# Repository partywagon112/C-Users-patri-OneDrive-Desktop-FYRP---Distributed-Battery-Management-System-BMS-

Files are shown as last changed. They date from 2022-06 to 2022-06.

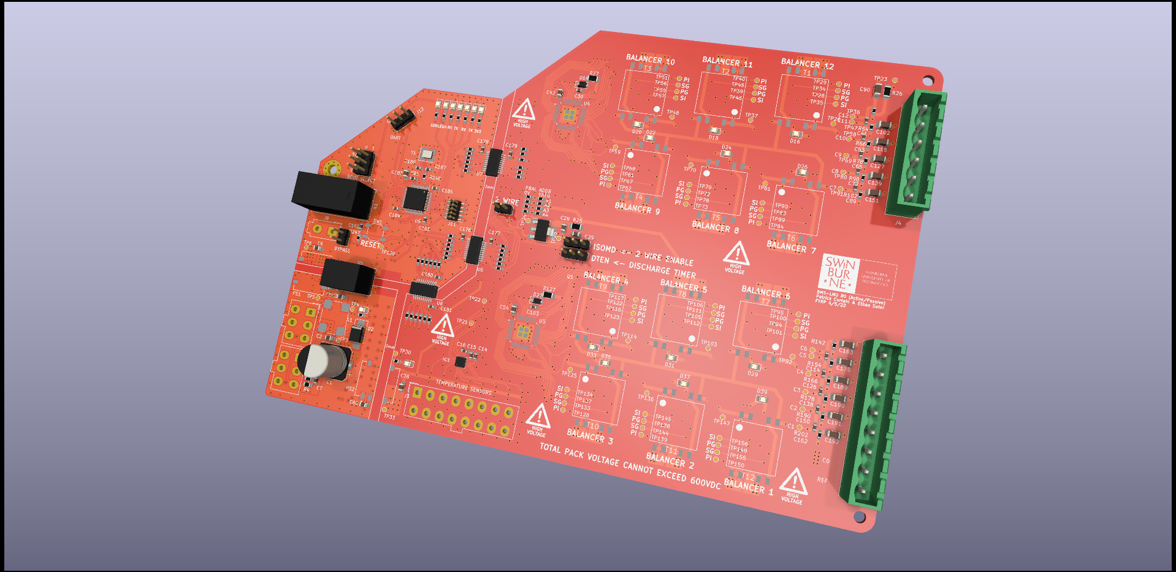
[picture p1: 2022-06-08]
Images/top side render.png

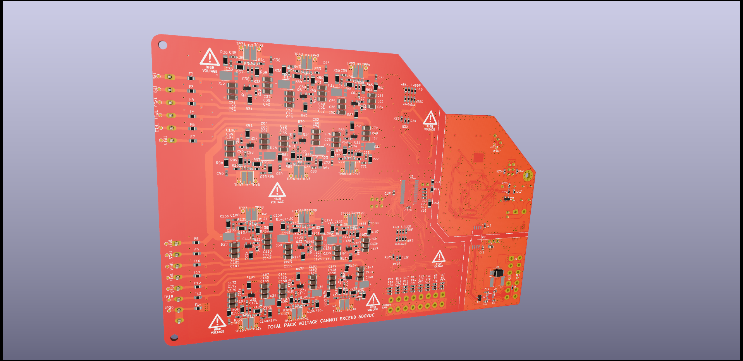
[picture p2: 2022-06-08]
Images/bottom side render.png

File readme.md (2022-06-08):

# Final Year Research Project - Distributed Battery Management System
## Design, Optimisation and System Integration for an Electric Solar Vehicle
### Patrick Curtain & Ethan Suter, Swinburne University of Technology

A project to design a battery management system as a testbed for how one would integrate an active balancing system for an electric vehicle, in particular, an electric solar vehicle.

In this project, a hypothetical system has been conceived for the Swinburne Solar Team electric vehicle and a BMS layed out for how it would function as part of the vehicle. The BMS in question is a multichemistry (0.8-5V), distributed system, comprised of a single gateway (Master) Central Management Unit (CMU) and multiple twelve cell circuit (Slaves) called Local Measurement Units (LMU), connected to the gateway on a private CANBUS. The project makes use of the LTC6811-2 and LTC3300-2, using conventional 4-Wire SPI to make the connection to a control interface more modular.

## BMS-LMU
BMS-LMU

As a proof of concept, a test LMU was produced to perform the specified functions of the BMS-LMU, and documentation included in this repo. This integrates the active and passive balancing units onto a PCB with an STM32F103 performing the local management and CANBUS forwarding functions.

## Acknowledgements
A big thank you to Team Swinburne for the platform and code base used throughout the design of this project. Their work is available: https://github.com/Team-Swinburne

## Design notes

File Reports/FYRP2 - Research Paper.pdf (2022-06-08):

# Distributed Battery Management System (BMS) Design, Optimisation, and System Integration for an Electric Solar Vehicle

## Research Paper - Final Year Research Project (ENG40001)

### Patrick Curtain

Swinburne University of Technology Melbourne, Australia
101109830@student.swin.edu.au

### Ethan Suter

Swinburne University of Technology Melbourne, Australia
102110833@student.swin.edu.au

Abstract—This paper proposes a battery management system that integrates an active balancing system in order to extend the lifetime time of an electric vehicle and minimise wasted energy. The system makes use of a central gateway that functions as the master, and a user configurable number of measurement taps in multiples of

### 12. Whilst there are many automotive grade BMS units

available, very few include an active balancing system, it is the goal of this project to create a template for one that optimises cost, physical space requirements, complexity, performance, and safety. The design context for this system is for the purposes of an SPEV (Solar Powered Electric Vehicle) intended for entry into the World Solar Challenge, however the technology is not limited to this application. Being able to maximise the amount of energy that is wasted is especially beneficial - as current generation EV battery systems age, the delta between the highest and lowest cells will increase, and being able to quickly balance out the issue on the go will prove to be a groundbreaking leap in technology.
Index Terms—SPEV, EV, BMS, Lithium Ion, Lithium Titanate, Electric Vehicles
I. INTRODUCTION
A Battery Management System (BMS) is one of the most important components of a lithium powered electric vehicle. They function to ensure the safety of the pack, preventing dangerous under/overvoltage conditions, preventing component damage and hazardous fail modes. As lithium batteries degrade, their electrical properties change and will charge and discharge at different rates.
The difference between the highest and lowest cell voltage is termed the pack delta, and the aim of balancing is to reduce it as much as possible, typically within the range of tens of milivolts. Battery packs that do not balance contain excess energy that cannot be discharged because if so, the minimum cell voltage will be exceeded [1]. Likewise, the same is true of charging, if the maximum cell voltage will be exceeded, then charging must cease.
The most common method of cell balancing is passive balancing, where the energy from the highest cell is discharged as heat. This practice is inherently wasteful and if the BMS is stored within the accumulator, this also serves as an unwanted source of heat for the pack, wearing the cells out further. Another issue of this strategy is that one is still limited by the lowest cell voltage - all cells are bled down to the lowest cell voltage, a poorly performing cell cannot have energy put into it. Passive balancing is slow, and slower if the thermal limits are exceeded.
Active balancing differs from passive balancing in that is is able to redistribute energy about the pack; higher cells are able to charge lower cells. This process reduces wasted energy and heat in the accumulator. In the case where there is a cell with poor health, it is then possible to siphon energy from this highest cell to extended the life of the pack.

II. BACKGROUND
The Swinburne Solar Team vehicle at present makes use of repurposed Lthium Titanate (LTO) cells acquired in 2018. Lithium Titanate cells have a nominal cell voltage of 2.3V, well below the minimal cell voltage supported by most commercially available BMS units. Furthermore, these cells are from several different sources; they discharge at vastly different rates. Whilst the project would likely transition to LFP (Lithium Iron Phosphate) based cells at a later stage, in the pre-competition phase of the project, budgetary constraints are an ongoing issue; it is likely that large cell deltas will prove to be an issue for some years to come. Cell measurement is not the only challenge in the scope of this design. The changing landscape of solar technology also provides quite a few issues for how to structure an architecture suitable for an extremely wide voltage range. At the moment, the most prevalent flexible cells have a low open cell voltage, around 5.6V [2]; these being connected in series to maximise their voltage output. The most successful cruiser class vehicles in the competition are medium voltage, around 90V to 220V. As this technology improves, it is likely that the voltage will increase rather than decrease to reduce mass [3], and as such, it is necessary to accommodate higher voltages, possibly as high as 400V or 800V. At this voltage, it is unlikely that LTO (Lithium Titanate) cells could be used, as the low nominal cell voltage would mean at least 285 cells would be required in series for 800V, with parallel units required for the extra current carrying and energy. It should be noted that LTO cells do typically support a higher cell current before experiencing failure, however it is unlikely this would not compensate for the extra capacity requirements.
A. Project Goals, Scope, and Research Questions With this context in mind, the following goals were set to guide the design of the system:
- Cell voltage range of at least 0.8V to 4.5V to meet the requirements of most lithium chemistries.
- Accommodate a total pack voltage of up to 600V.
- There should be no unpopulated cell measurement taps; with fewer cells the BMS should be reduced in size.
- Able to manage cells in poor health as efficiently as possible; the reduction of energy waste in balancing.

With so few automotive grade BMS units offering active balancing, this project addresses the gap in research into the feasibility and practicalities of including an active cell balancing system. The primary questions are as follows:
- Is the amount of space required to include an active balancer suitable in such a weight optimised vehicle.
- Is it possible balance the vehicle on the go to extend the life of vehicle.
- How would one approach the design of such a BMS system, and ensure it meets ISO26262 requirements.
- What efficiency gains can this system provide over typical passive-only solution on the market currently?

III. METHODOLOGY
A. State of Charge Estimations
After initial research of existing ways to estimate state of charge early on in the project, it was decided to use a combination of cell voltage readings and coulomb counting [4].
Further research into the cell chemistry available to use for this project (LTO) demonstrated potential challenges with voltage-level based estimations. An LTO discharge graph shown in Figure 1. While the non-linearity is not of direct concern (creating a map of voltages to correspond to charge levels would be trivial), it does result in a large portion of the cell’s discharge cycle occurring over a relatively small voltage delta. This itself can be mostly accounted for but the additional presence of voltage sag complicates this characteristic. A cell experiencing a high current draw that starts to lessen whilst in a shallow-sloped region of its discharge curve could read approximately the same voltage level for 10-20% of the cell’s capacity. Accounting for voltage sag could be done formulaically by establishing a mathematical relationship between the amount of voltage sag occurring at a given capacity level and the amount of current being drawn through that cell [5]. Even accounting for voltage sag, using only instantaneous measurement based estimation will result in SoC readings fluctuating in a dynamic charging/discharging environment. Accurately accounting for voltage sag while current draw changes constantly is a much more difficult task.

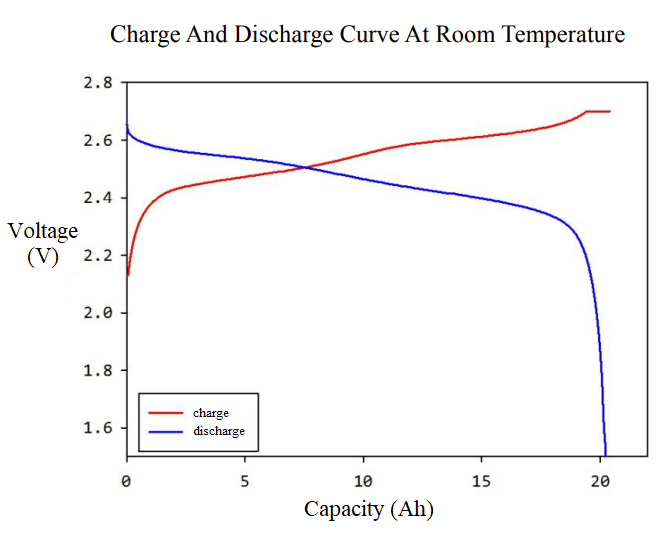
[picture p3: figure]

Fig. 1: Discharge graph of an LTO cell. Note the low cell voltage range. Sorce: data sheet for 16Ah LTO cells in use by the Swinburne Solar Team [6].

Coulomb counting can be achieved by attaching a current clamp to the output, measuring the instantaneous power discharged overtime, and integrating this to find how much energy has been consumed and compare to the pack’s theoretical capacity. Coulomb counting can provide a stable SoC estimation over time, reading cell voltage and current draw multiple times a second and extrapolating energy used. Coulomb counting will result in far more meaningful SoC readouts during periods of high/fluctuating current draw. A drawback of this method is that it can drift over time, due to not being able to account for energy wasted as heat and a lack of absolute reference. In nautical terms, this method is analogous to dead reckoning.

With these two estimations of the packs health, a weighting can be applied to the validity of each estimation. With high current discharge, the effect of voltage sag can be mitigated by relating current discharge to the weighting of the coulomb counting method; During periods of high current draw the coulomb counting estimation will be weighted more.

After this methodology has been implemented in the BMS a formula will have been developed to represent stage of charge.

B. Modular Stack Design

In order to achieve the target of space optimisation, a distributed architecture was pursued to provide scalable device size across different battery configurations. This architecture abstracts away the functionality of the BMS chips, making it simpler to change out modules, iterate designs, and refine the project further.
A similar modular architecture is explored by Henar Cailang, Caliway, and Wanson, for a small form BMS for use in a Motorbike, using a masterslave system [7]. Similarly, the BMS concept of this project is to be designed is broken up into the same style of system, with a Central Management Unit (CMU) as the gateway that oversees many Local Measurement Units (LMU), which each attend to a particular group of cells. The main disadvantage of this scheme is that fault detection becomes inefficient, as communication becomes reliant on persistent updates between units, requiring a watchdog, and whilst the absence of a module may not mean a fault, one shall be triggered, and little more information can be gained [7].
C. Cell Measurement, Active vs. Passive Balancing, and ASICs

Passive balancing is conceptually quite simple; Whilst a battery is charging, the highest cell is discharged to match the lowest cell, and this process repeats until all are within a certain delta. This is achieved by simply discharging energy from the cell as heat, light, or kinetic energy, etc.
Active balance utilises the excess energy from the highest cell to charge the lowest cell. In this way, energy has been redistributed, not lost, thus minimising wasted energy. This is usually achieved with some form of coupling, to connect the highest to the lowest cell, and using that to equalise the two cells. This is usually done by isolating both cells from the stack, and connecting them in parallel, with circuitry that allows the control of current flowing between the cells to prevent large loads causing degradation for both cells involved. In addition to gains in energy conservation this method can also achieve more than double the effective rate of balancing, since the two most outlying cells are being equalised to an average cell voltage simultaneously, rather than one cell being discharged all the way down to the lowest cell voltage at a time.
In order to simplify the complexity and overall size of the final output, it was decided very early into the project, that a pre-designed BMS IC would be used. These ASICs typically integrate various forms of cell measurement to autonomously perform balancing with little external input required. Two ICs were sought to solve this issue, based on research from an earlier literature review [4], the LTC6811, and the LTC3300. These two BMS ICs are designed to work together to achieve the passive and active balancing requirements outlined for this project [8].

IV. DISCUSSION

Given cost and time restraints, the project was reduced in scope from it’s original plans such that a only the LMU would be designed, and a single functional LMU be produced to serve as a proof of concept. The LMU is the most important part of this project, representing the most complex amount of circuitry and the largest portion of functionality (for both hardware and software). The CMU’s functionality can be containerised in software; it can be simply a CANBUS gateway with some high side drivers to run the contactors, and simulating its functionality would be relatively trivial.

A. Active Balance Circuit Design
The active and passive circuits follow the design recommendations outlined by the manufacturer of the ASICs [9] [8], The passive circuit makes use of a small P-Channel FET that is able to handle around 100-500mA, and a small resistor. A LED circuit has been added to indicate which cells are balancing. The active balance circuit requires two high current switching FETs, with the secondary of each transformer being connected to a common charge rail(denoted as BOOST in the schematic). To help decrease the BOM, a dual channel N-FET with a low RDS, and low gate capacitance was used. These FETs will switch at a frequency of 2kHz, with a typical charge current of 2-4A. The way in which this circuit operates, is that the primary side of the highest voltage cell’s module will be coupled onto the secondary side. At the same time, the lowest cell’s primary coil will be switched at high speed to enable current flow. The LTC3300 manages this control loop, and a small measurement tap is attached to a shunt resistor connected to the drain of each FET, closing the control loop and providing the required hysteresis. The port on the right extends to the active and passive cell measurement inputs, and makes use of a simple RC filter to the adjacent cell (Cell measurements are differential), and the ground reference.

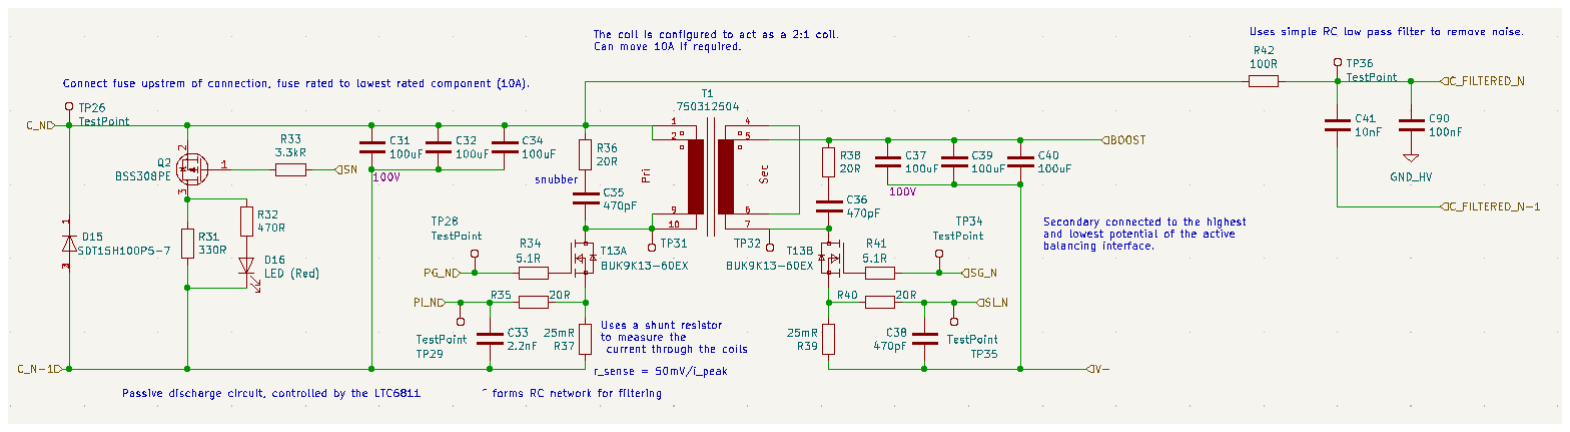
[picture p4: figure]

Fig. 2: The circuit used on each cell input, the left part includes reverse protection diode, and the passive balance circuit, a small SOT23 P-Channel FET, and a 330Ω resistor. The right half includes an isolated 2:1 10A transformer and N-Channel FETs with a connection to the boost rail.

B. PCB Design

The PCB for the LMU is significantly larger than original concepts for the design earlier in the project. The original idea was to create a daughterboard with a SODIMM form factor that would hold either 2(single-sided) or 4(double-sided) active balancing modules, that would connect to a backplane that would attach directly to the terminals of the cells [4]. in this way, should the active system be too large, modules could simply be removed.

C. Isolation, Safety, and Grounding

Grounds serve two main purposes, for protecting the integrity of signals, and protecting systems and users in case of a fault [10]. In the vehicle, an IMD (Isolation Monitoring Device) is used to ensure that no more than 2mA is able to pass from the high voltage system into the vehicles system. A device such as the ISOMETER IR155-3204 will be connected with the ability to break power to the main accumulators on fault [11]. This protects against the mechanical failure of various parts of the powertrain, where contact is made when insulation

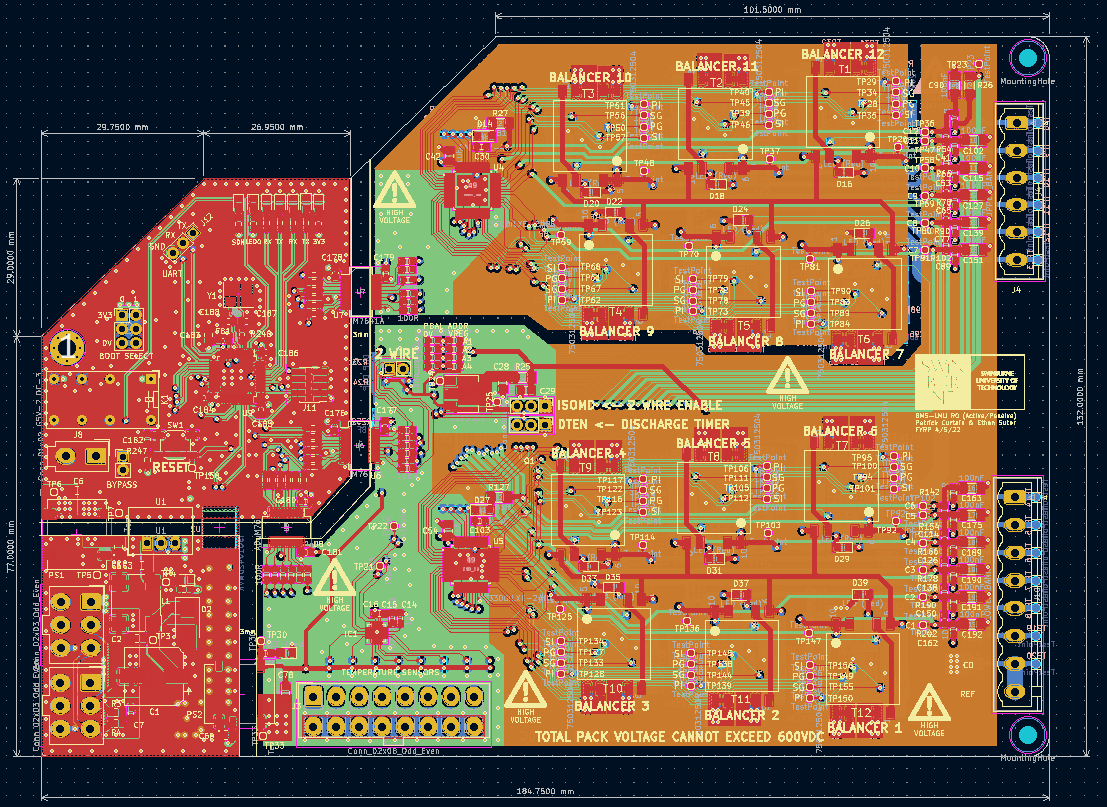
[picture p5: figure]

Fig. 3: The PCB designed to perform the functions described by the LMU.


Fig. 4: Rendering of the top side of the LMU PCB.

is not present or has fatigued, as well as the electrical failure of the various ICs and DC-DC converters that are used to isolate the barrier.
Of great concern in the development of this BMS was its ability to handle high voltages. A safety isolation barrier of 3mm has been included to allow the device to meet the IPC2221B high voltage clearance requirements [12].
In order to simplify the architecture and avoid being locked into using Linear Technology’s proprietary interpretation of SPI, isoSPI, a simple series of simple high speed digital isolators is to be use. The primary advantage of this scheme is that inter stack connections do not need to be adjacent since the communication interface is connected to the same ground as the vehicle. As such, the pack can be split across the vehicle without much additional wiring. There is some danger associated with extending the ground planes used for high voltage. A large

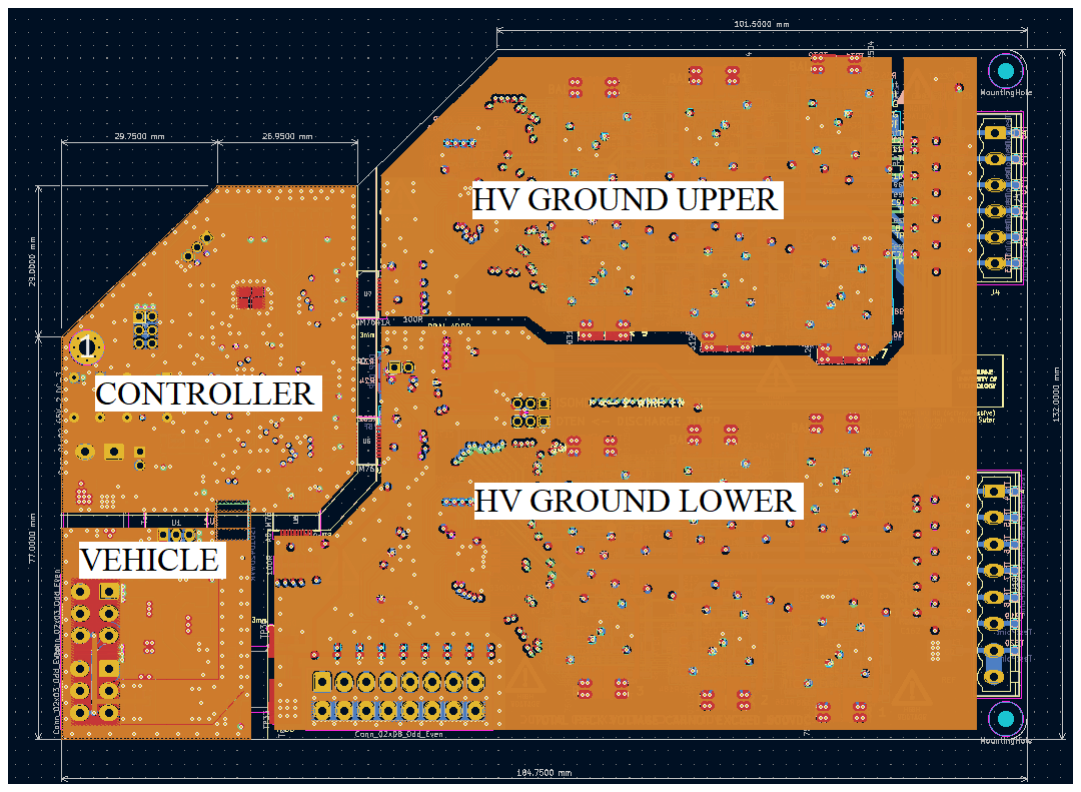
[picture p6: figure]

Fig. 5: The different ground planes used to break up the PCB. Note that each of these zones is galvanically isolated except for HV ground upper and lower, explained in Section IV-D.

plane is a huge physical target and risks the operator or assembler making contact with the high voltage plane. Of course, during assembly, high voltage gloves must always be warn and ample warnings are listed on both sides of the board, however additionally, these planes have been restricted to the internal layers of the PCB. Therefore the risk is reduced to only traces and components.

D. EMC Considerations

There are several issues that face the design of the HV system; balancing cost, physical size, and ensuring board maintains good electromagnetic immunity. The active balancers switch high currents at a relatively high frequency, as such they pose a risk to the other ICs as they will be the primary source of noise affecting cell measurement. The emissions of the device will directly affect the immunity of the other ground. The standard defence against this issue is to increase the size of the return path, and place that as close as possible to the signal. All signal layers are directly adjacent to a ground layer to minimise issues [3].
A small RC filter is utilised on the board. Due to space constraints, this was placed at the input of each voltage tap to the board, however the way to best optimise the strength of the filter would be to place it as close as possible to the input of the cell measurement IC.
The highest six cells of the stack are referenced relative to two points. The first reference is for the cell measurement the lowest potential of the stack. Whilst measurements are performed in a differential manner, the passive balance IC itself is grounded to the lower potential ground, and as such lines to the point, must be shielded to that ground. The second ground is relative to the reference of the sixth cell in the stack.
A proposed alternative strategy was to make use of a six layer stackup, with the cell signal layer being adjacent to a layer for the active ground, and another layer dedicated to only the HV ground. This was dismissed to reduce cost.
There is an additional ground included on each LMU that is galvanically isolated from the vehicle ground and the HV ground, that contains the microcontroller and logic. This is done to provide an extra level of immunity for the mission critical microcontroller. This practice is well endorsed by SAE design guidelines as it provides a good way to break up critical areas of the vehicle [3]. Even in the case of a communication failure with the rest of the vehicle, the microcontrollers integrity must be maintained. Given the high amount of switching noise generated by the powertrain, one should expect immunity to be an issue. CISPR 25 is the typical automotive standard that is used to quantify how much the device radiates, and its immunity [13], and as testing progresses, some parts of this regime may be tested to gain insight into the performance of the design.
V. CONCLUSION
With the testing of the LMU commencing in the next week on a live battery stack, it will be interesting to begin qualifying and quantifying the proposed solution. The challenges to reach this point have been great, with an underestimation of the space required for the additional active balancing circuitry being the primary issue, and causing the most delay. As discussed earlier, a good proposal would be to build a system where it is possible to remove the active balancing circuitry where not required. This has several advantages, such as minimising the width and length of the PCB, in exchange for better using the height, a usually under utilised part of the volume.
Various logistical issues have greatly affected component selection on the PCB, and as such, many parts have been interchanged since the initial schematic conception in late 2021. In its current state however, this project is close to producing a system that is able to outperform many of the automotive BMS that are available, and maximise the running time of the solar powered electric vehicle it which it will be used.

REFERENCES

[1] J. Cao, N. Schofield, and A. Emadi, “Battery balancing methods: A comprehensive review,” in 2008 IEEE Vehicle Power and Propulsion Conference. IEEE, 2008, pp. 1–2.
[2] M. A. Green, K. Emery, Y. Hishikawa, W. Warta, and E. D. Dunlop, “Solar cell efficiency tables (version 45),” Progress in photovoltaics, vol. 23, no. 1, pp. 1–9, 2015.
[3] S. Davis, Managing electric vehicle power, ser. SAE Deep Dive. Warrendale, Pennsylvania: SAE International, 2020.
[4] C. P. Suter, E., “Distributed battery management system (bms) design, optimisation, and system integration for an electric solar vehicle - progress report,” 2021.
[5] J. Chiasson and B. Vairamohan, “Estimating the state of charge of a battery,” IEEE Transactions on Control Systems Technology, vol. 13, no. 3, pp. 465–470, 2005.
[6] “Osn power: Lmo/lto datasheet 16ah (13110216),” 2010.
[7] H. M. O. Canilang, A. C. Caliwag, and W. Lim, “Design of modular bms and real-time practical implementation for electric motorcycle application,” IEEE transactions on circuits and systems. II, Express briefs, pp. 1–1, 2021.
[8] “Ltc6811-1 datasheet,” 2022. [Online]. Available: https: //www.analog.com/en/products/ltc6811-1.html
[9] “Ltc3300-2 datasheet,” 2022. [Online]. Available: https: //www.analog.com/en/products/ltc3300-2.html
[10] H. W. Ott, Electromagnetic compatibility engineering, ser. Wiley Online Library ebooks. Hoboken, N.J: John Wiley Sons, 2009.
[11] “Bender isometer ir155-3203/ir1553204 datasheet,” 2022.
[Online]. | Available: | https://www.bender.de/en/products/
insulation-monitoring/isometer ir155-3203ir155-3204 (https://www.bender.de/en/products/insulation-monitoring/isometer_ir155-3203ir155-3204)
[12] T. G. D. 31b) of the Rigid Printed Board Commitee (D-30) of IPC, IPC-2221B: Generic STandard on Printed Board Design. IPC, 2012. [Online]. Available: https: //www.ipc.org/TOC/IPC-2221B.pdf
[13] V. Rodriguez, “Automotive component emc testing: Cispr 25, iso 11452-2 and equivalent standards,” IEEE electromagnetic compatibility magazine, vol. 1, no. 1, pp. 83–90, 2012.

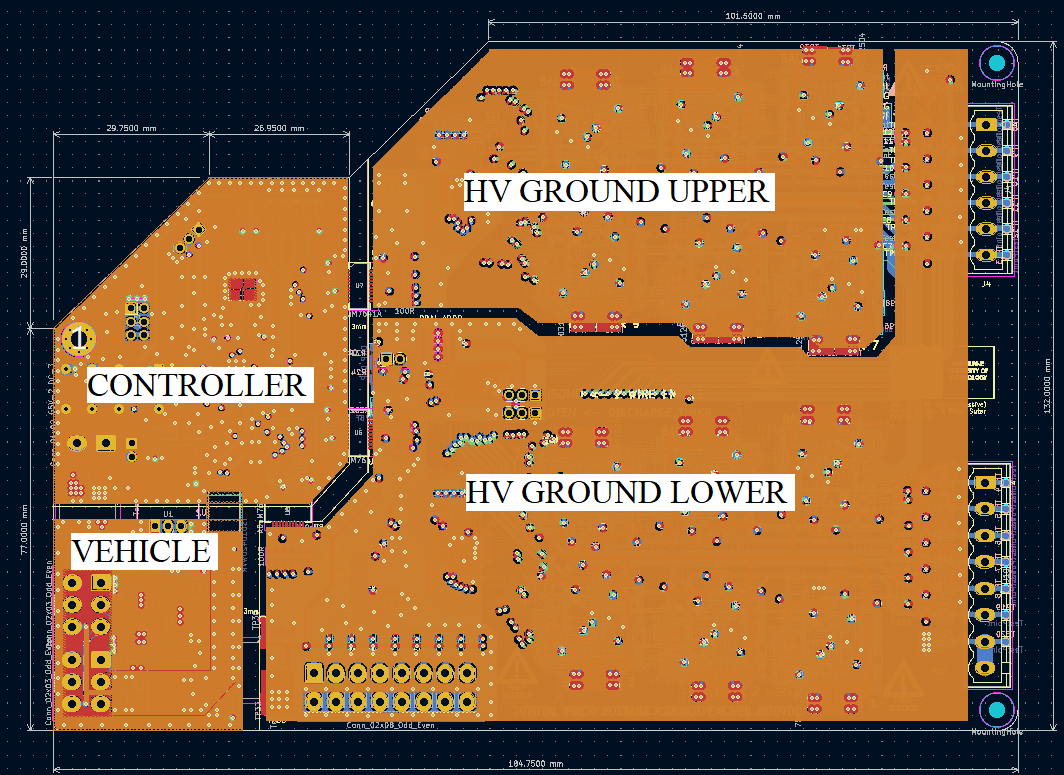
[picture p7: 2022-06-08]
Images/ground strategy labelled.png

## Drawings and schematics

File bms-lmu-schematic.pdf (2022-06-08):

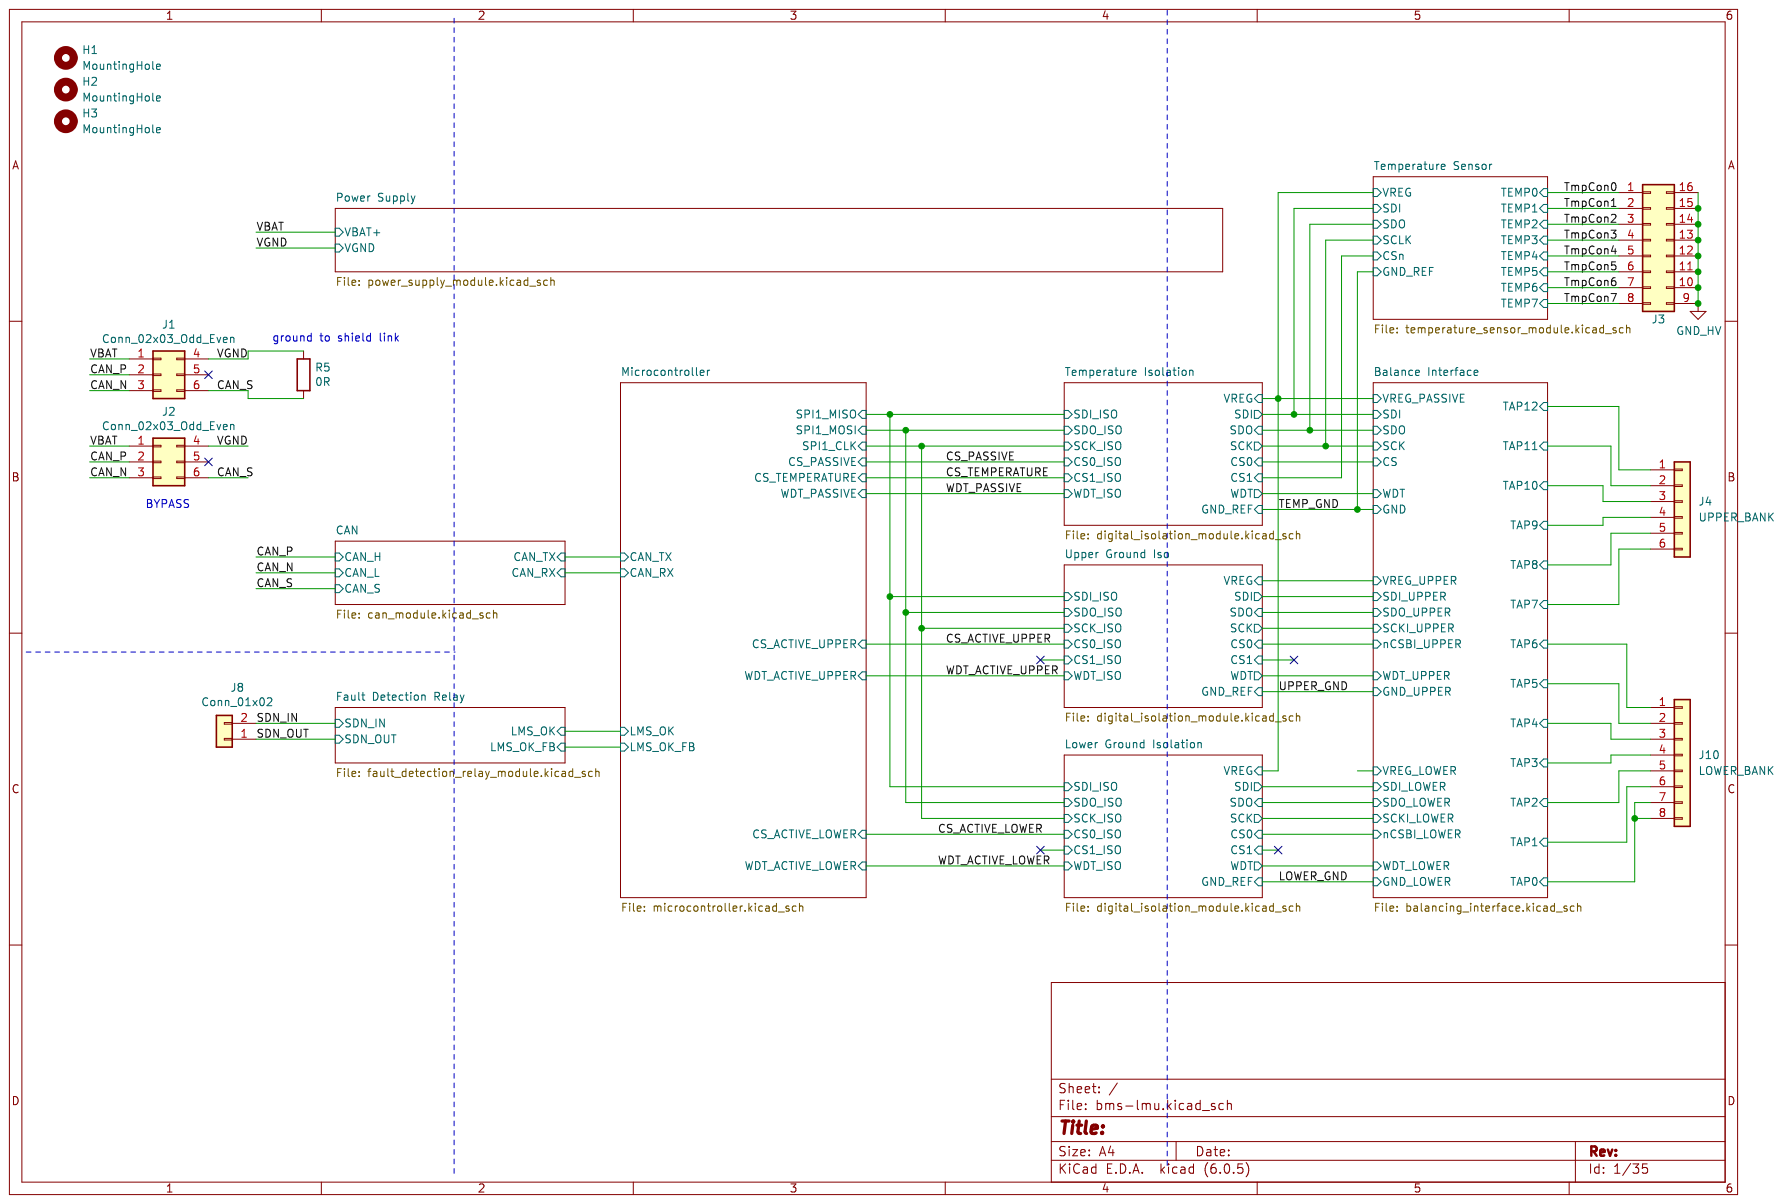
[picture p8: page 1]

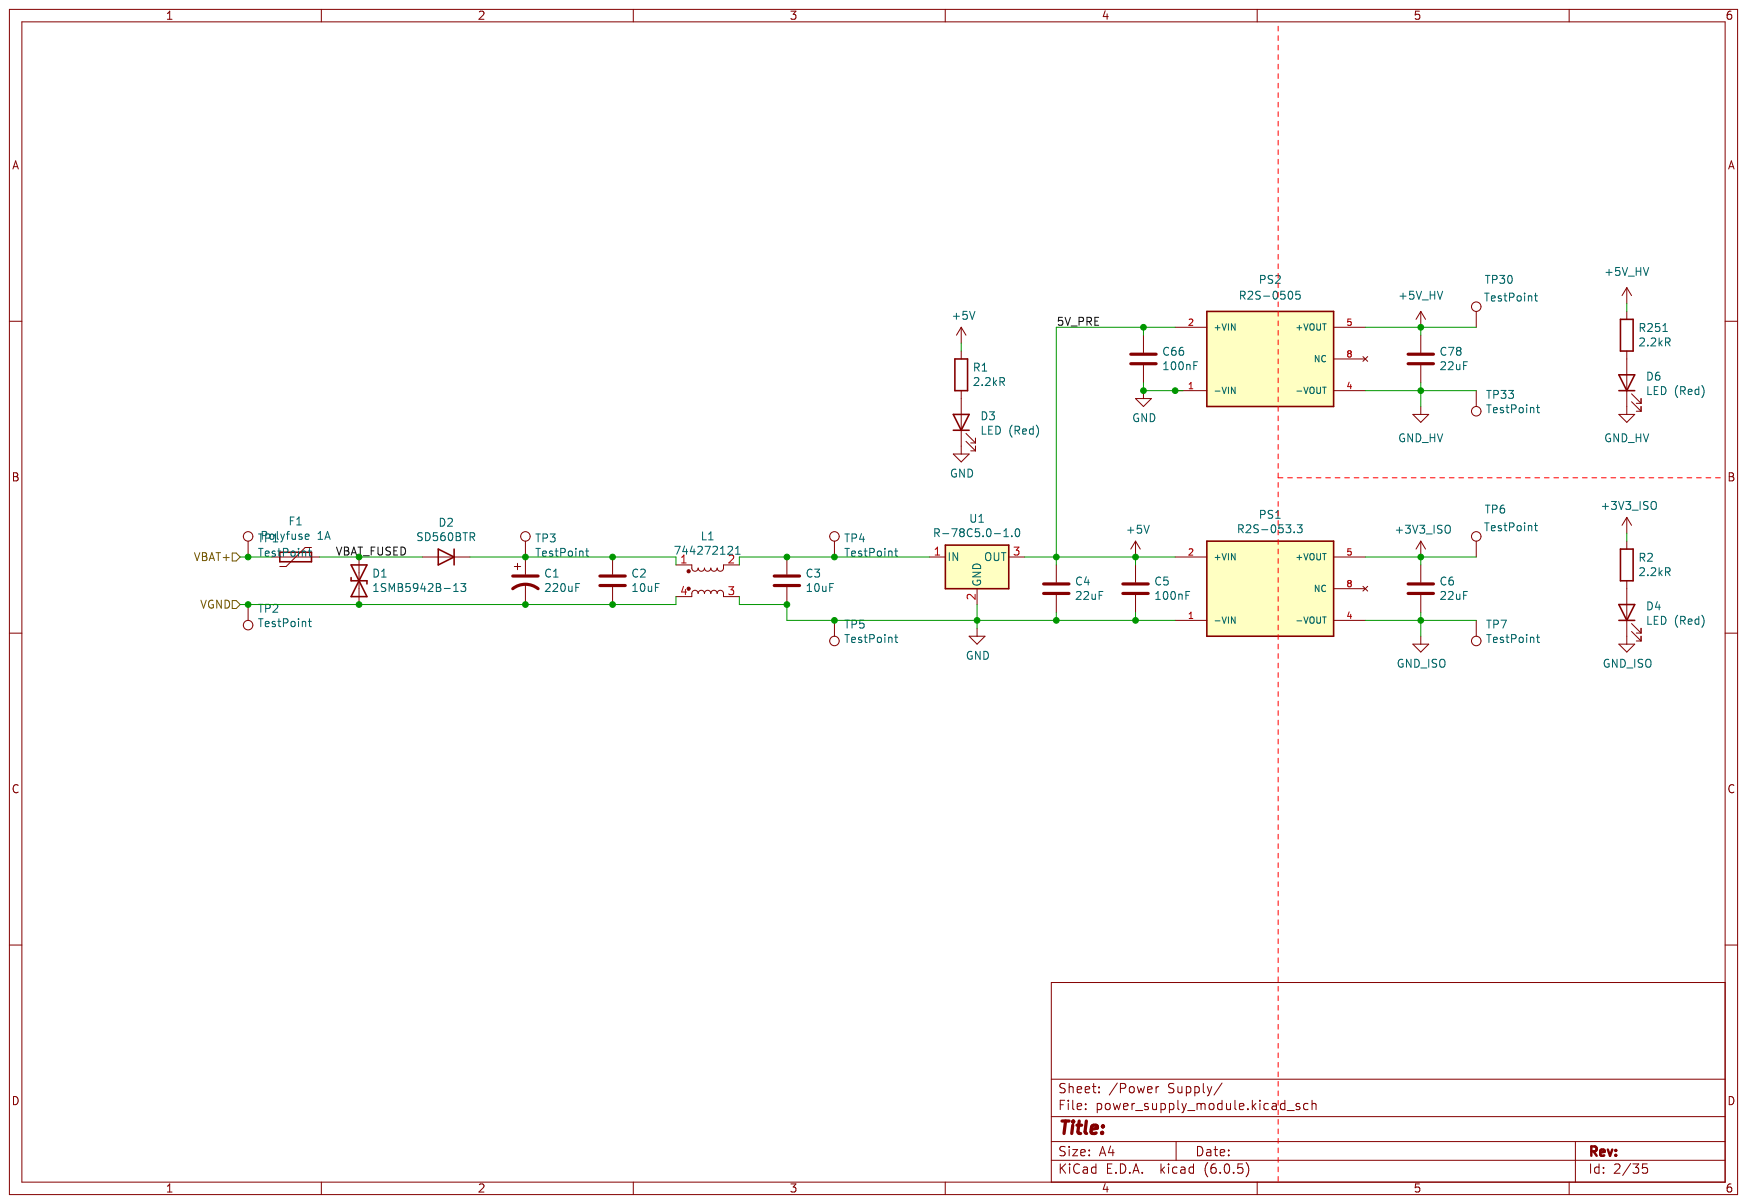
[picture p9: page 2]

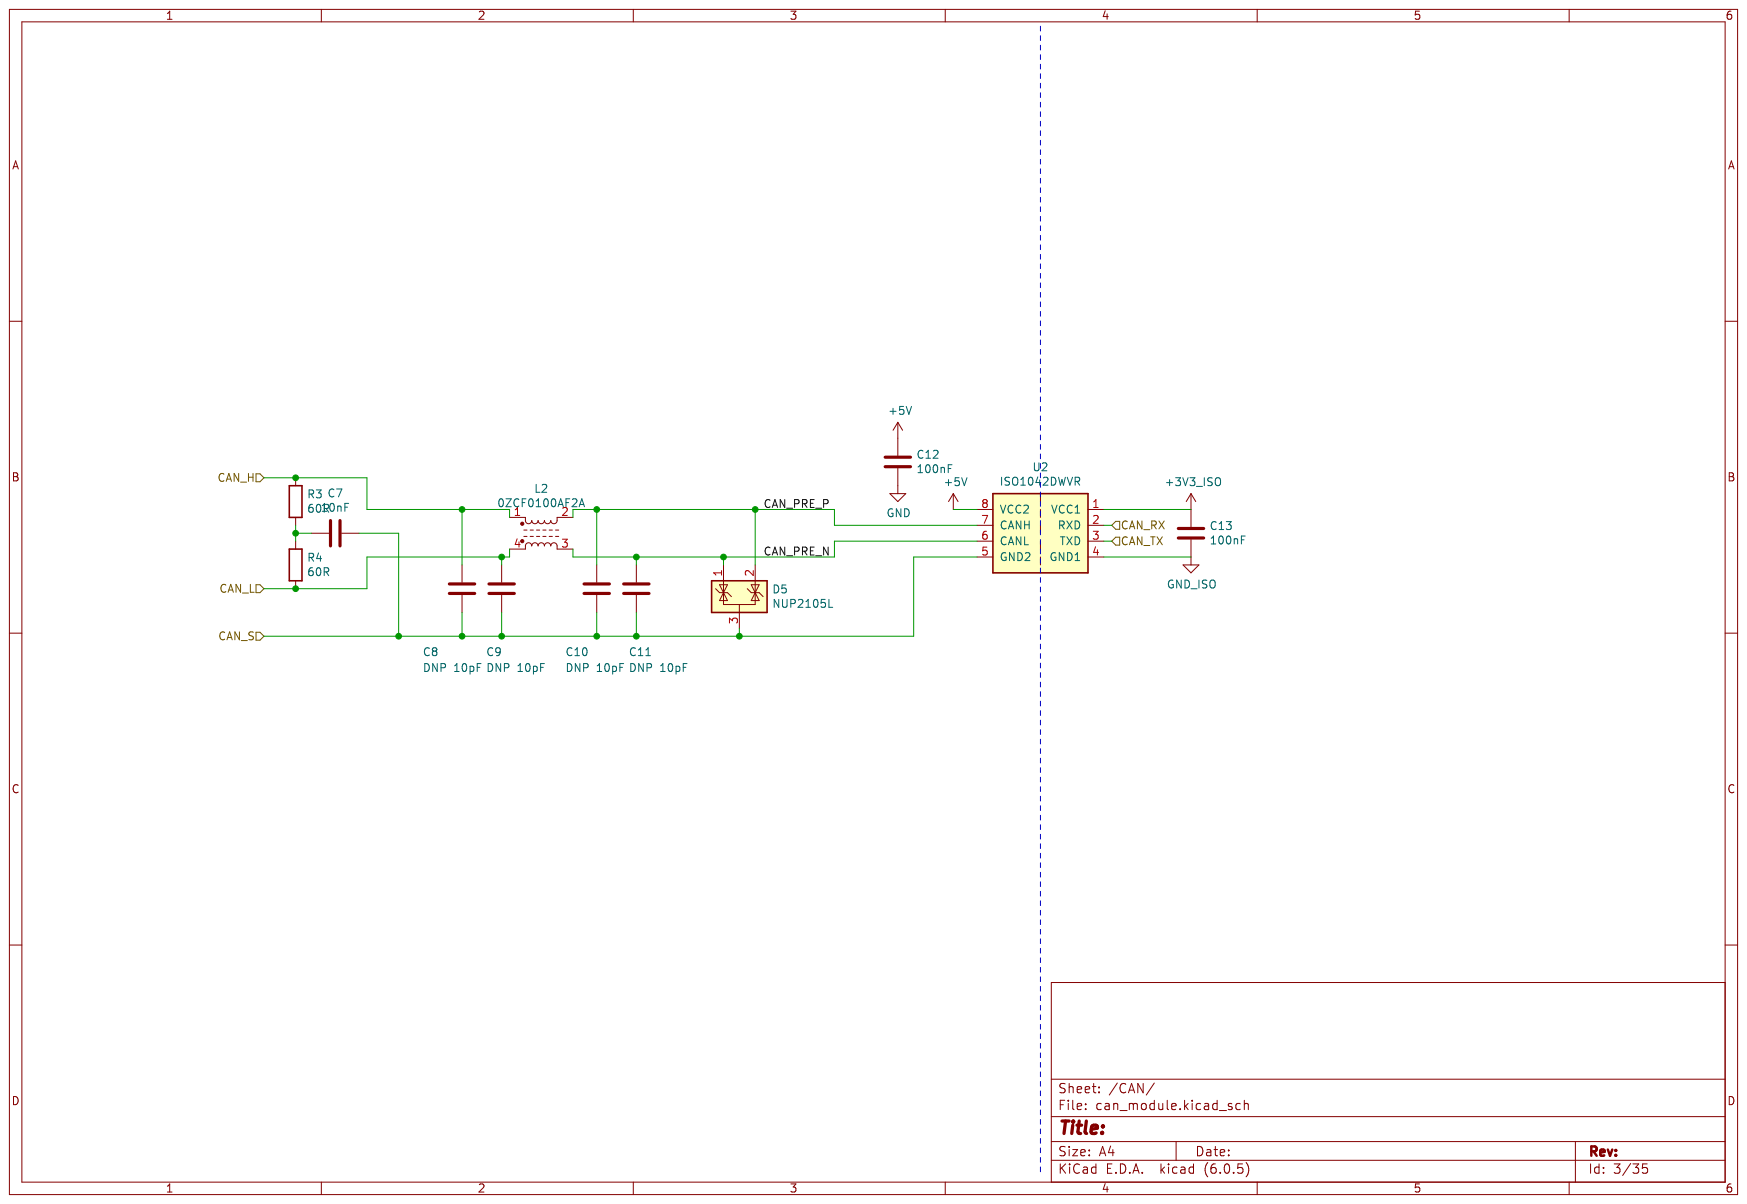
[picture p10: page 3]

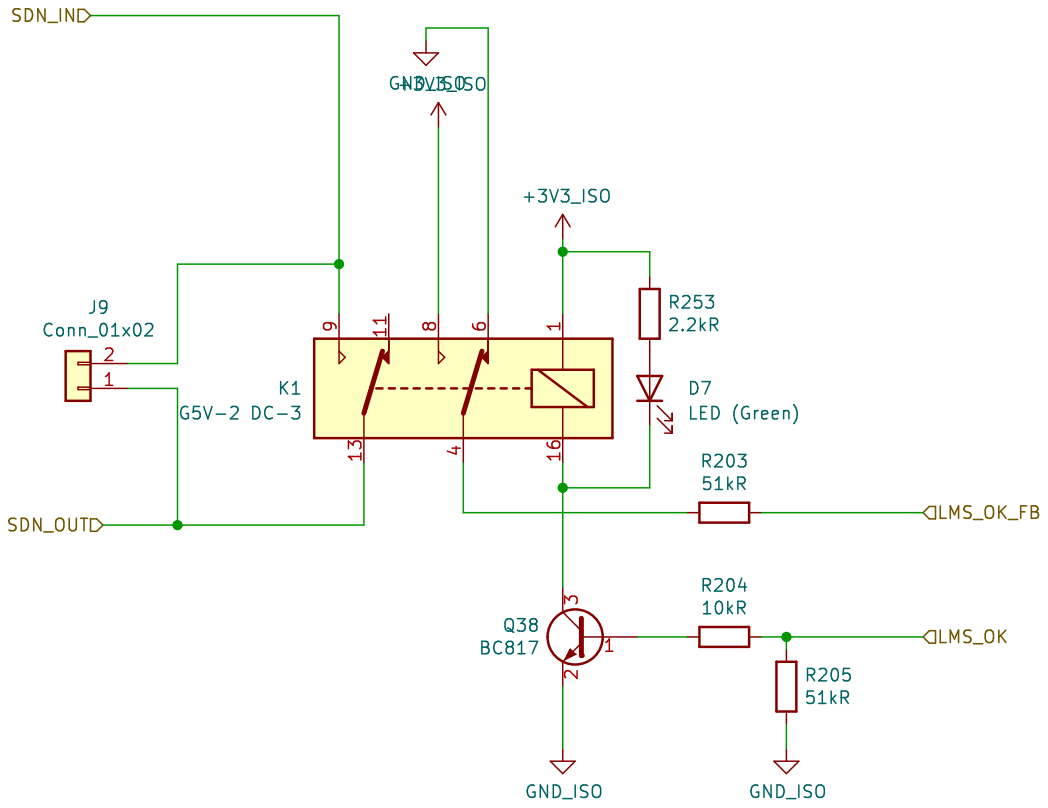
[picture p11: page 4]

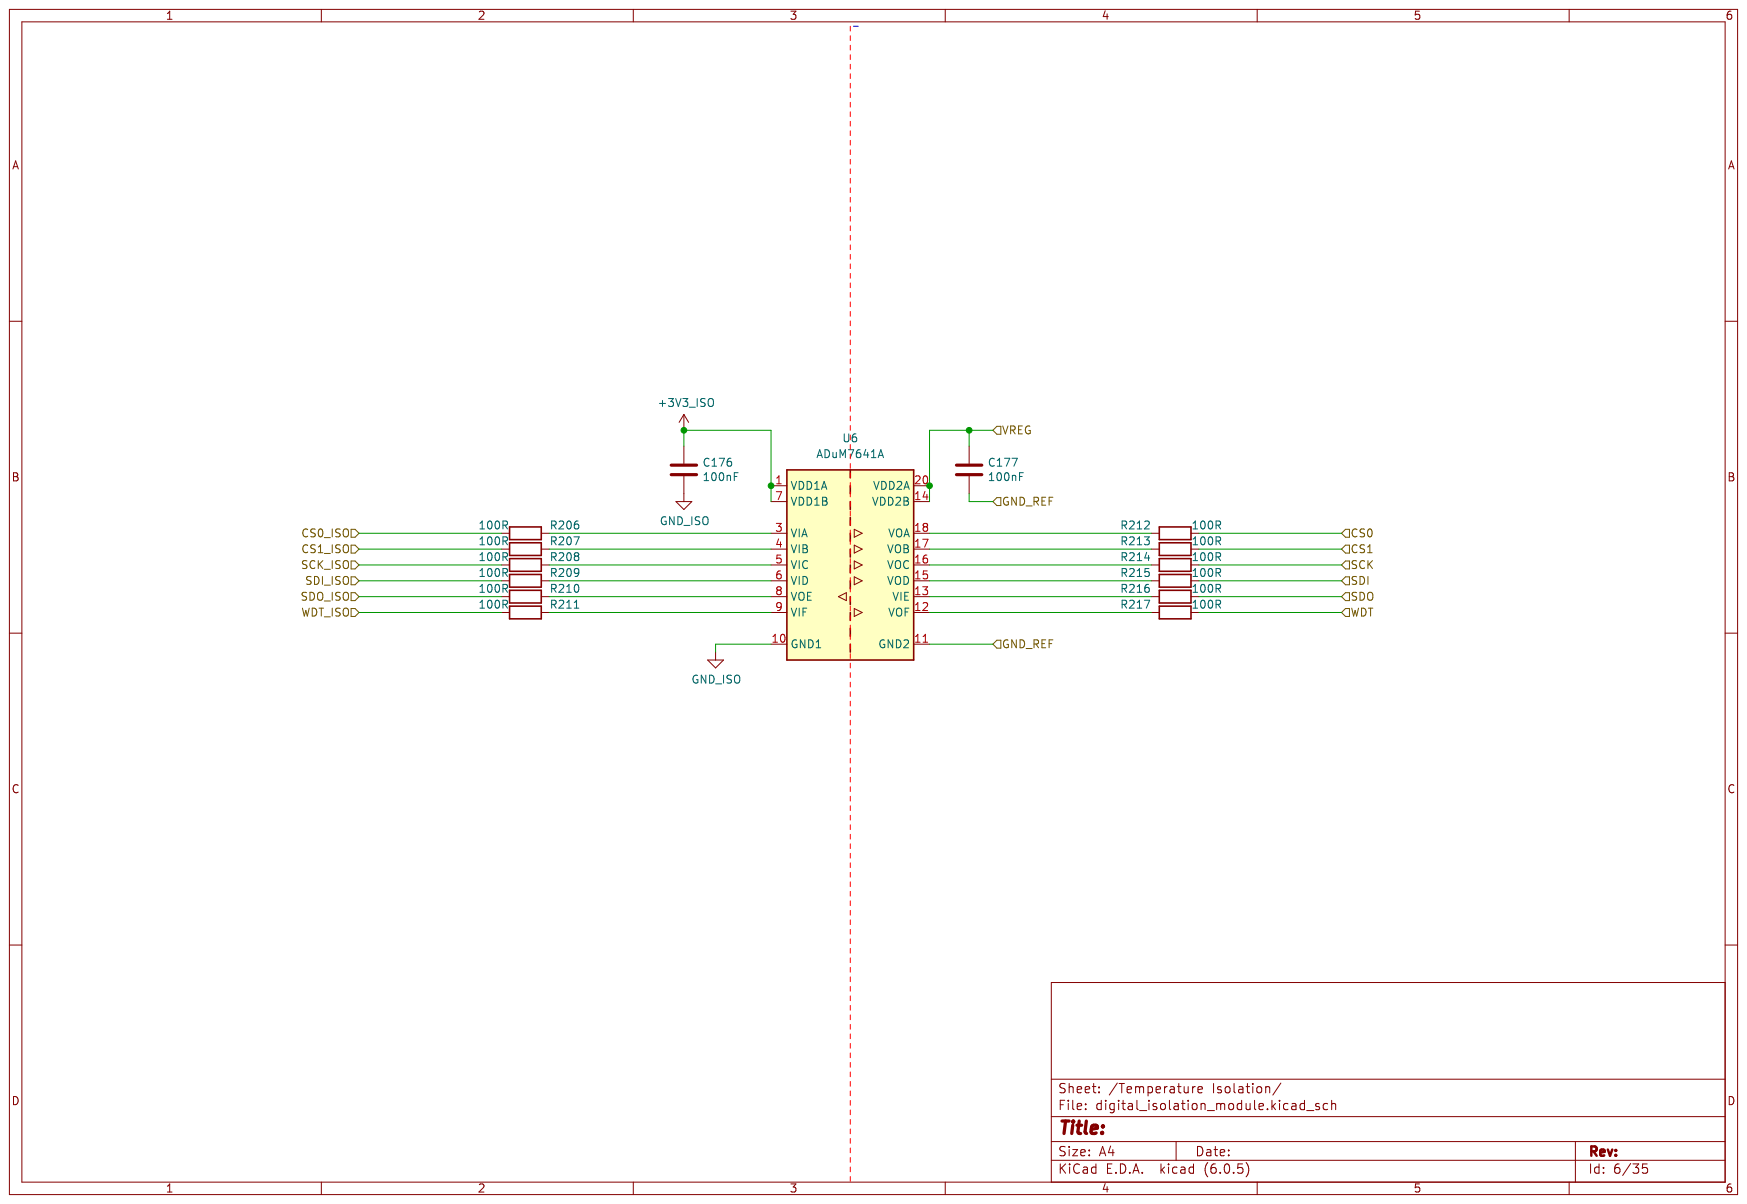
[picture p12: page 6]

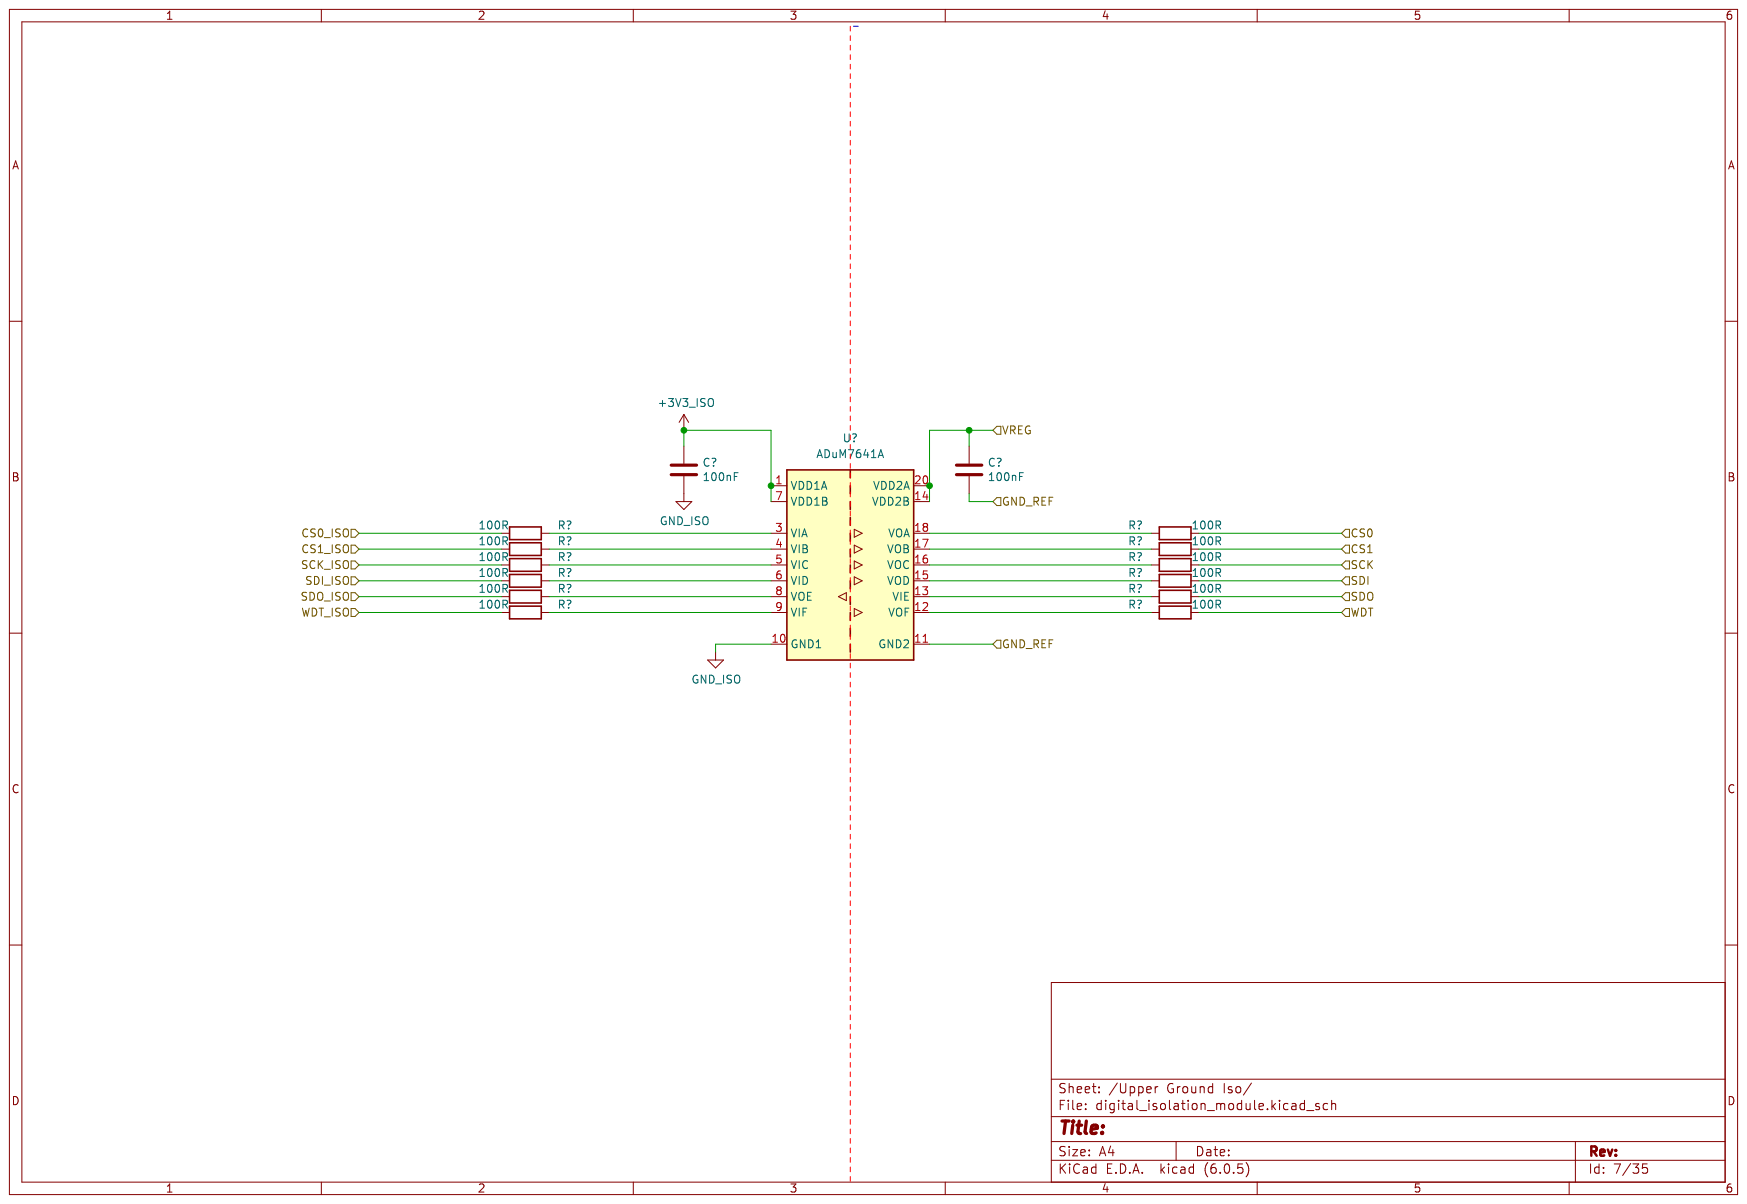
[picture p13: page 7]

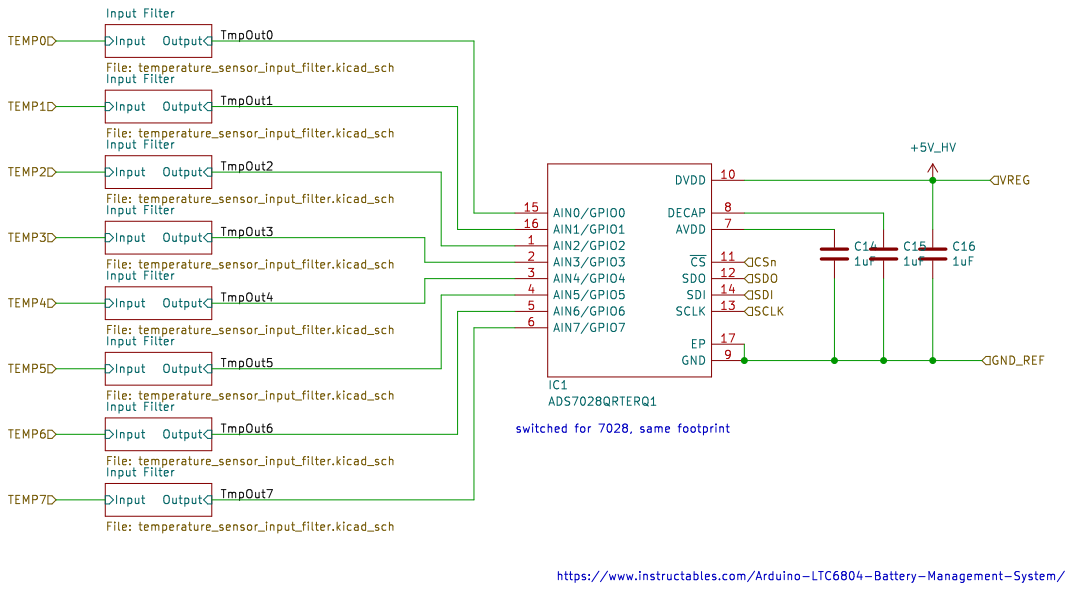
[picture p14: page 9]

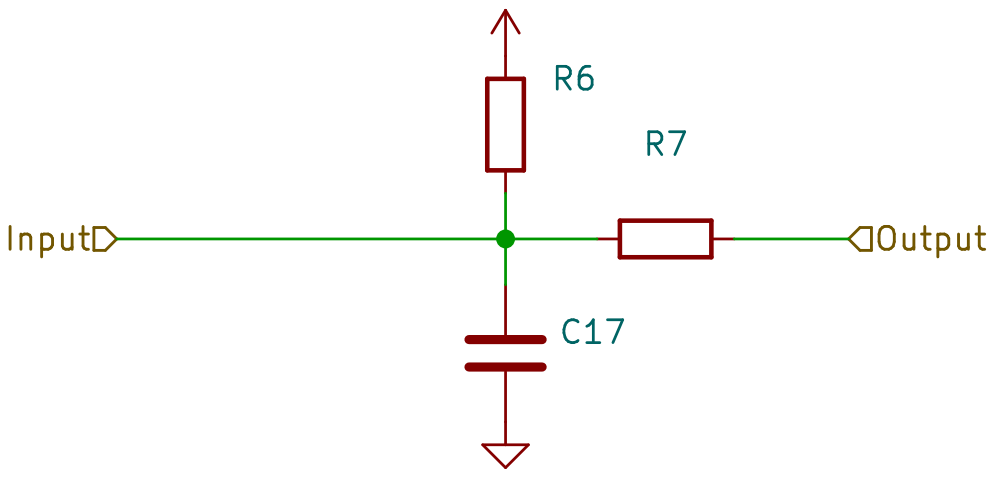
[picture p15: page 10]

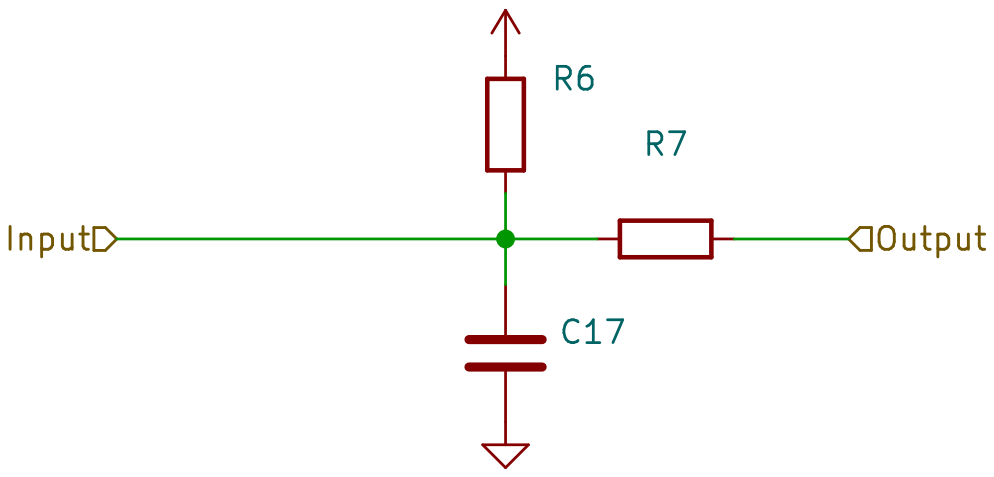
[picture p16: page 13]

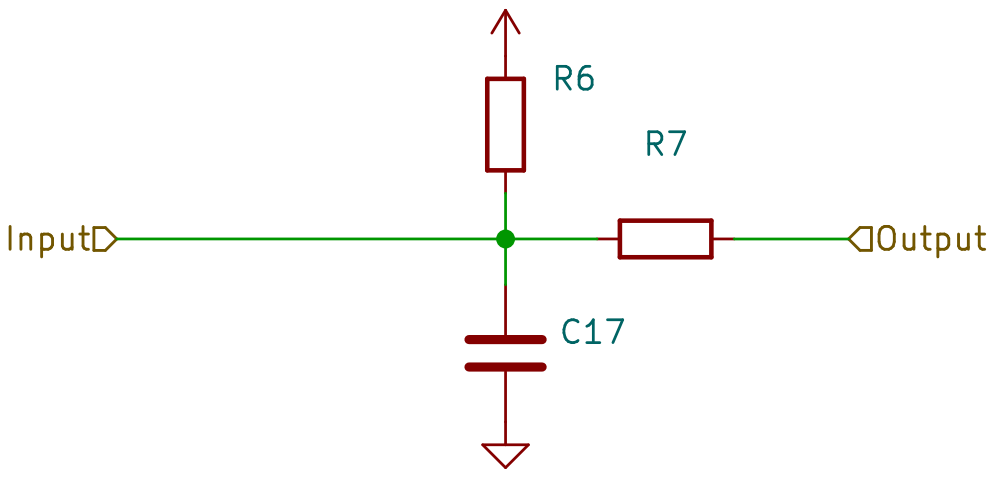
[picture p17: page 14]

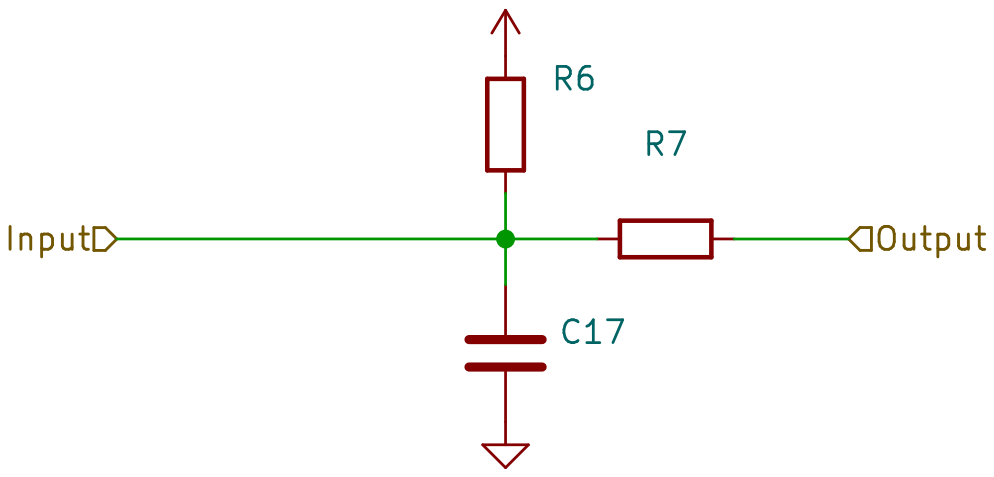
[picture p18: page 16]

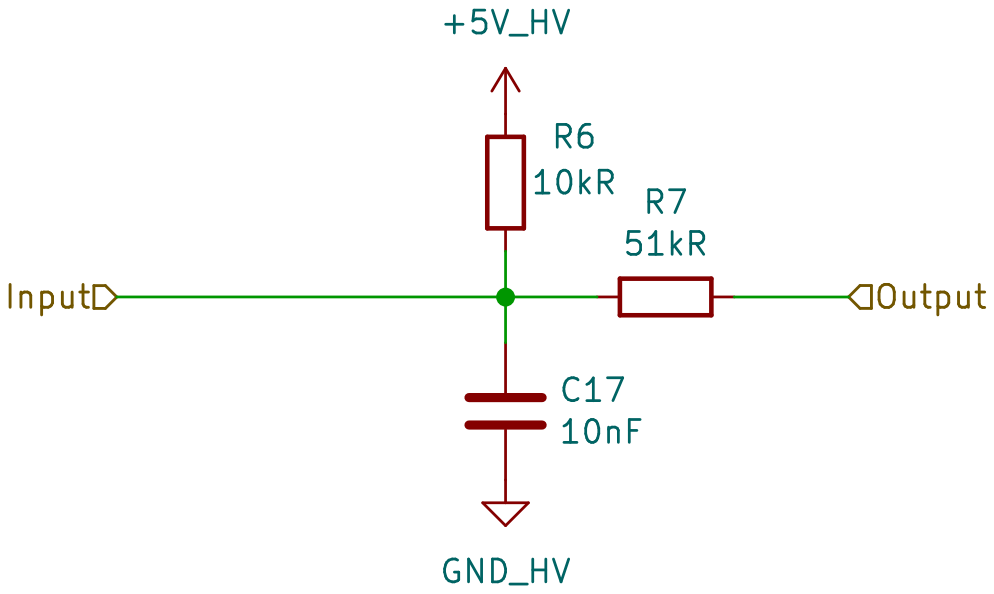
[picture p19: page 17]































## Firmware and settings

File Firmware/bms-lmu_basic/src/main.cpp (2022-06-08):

/*! Analog Devices DC2259A Demonstration Board. 
* LTC6811: Multicell Battery Monitors
*
*@verbatim
*NOTES
* Setup:
*   Set the terminal baud rate to 115200 and select the newline terminator.
*   Ensure all jumpers on the demo board are installed in their default positions from the factory.
*   Refer to Demo Manual.
*
*USER INPUT DATA FORMAT:
* decimal : 1024
* hex     : 0x400
* octal   : 02000  (leading 0)
* binary  : B10000000000
* float   : 1024.0
*@endverbatim
*
* https://www.analog.com/en/products/ltc6811-1.html
* https://www.analog.com/en/design-center/evaluation-hardware-and-software/evaluation-boards-kits/dc2259a.html
*
********************************************************************************
* Copyright 2019(c) Analog Devices, Inc.
*
* All rights reserved.
*
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
* THIS SOFTWARE IS PROVIDED BY ANALOG DEVICES "AS IS" AND ANY EXPRESS OR
* IMPLIED WARRANTIES, INCLUDING, BUT NOT LIMITED TO, NON-INFRINGEMENT,
* MERCHANTABILITY AND FITNESS FOR A PARTICULAR PURPOSE ARE DISCLAIMED.
* IN NO EVENT SHALL ANALOG DEVICES BE LIABLE FOR ANY DIRECT, INDIRECT,
* INCIDENTAL, SPECIAL, EXEMPLARY, OR CONSEQUENTIAL DAMAGES (INCLUDING, BUT NOT
* LIMITED TO, INTELLECTUAL PROPERTY RIGHTS, PROCUREMENT OF SUBSTITUTE GOODS OR
* SERVICES; LOSS OF USE, DATA, OR PROFITS; OR BUSINESS INTERRUPTION) HOWEVER
* CAUSED AND ON ANY THEORY OF LIABILITY, WHETHER IN CONTRACT, STRICT LIABILITY,
* OR TORT (INCLUDING NEGLIGENCE OR OTHERWISE) ARISING IN ANY WAY OUT OF THE USE
* OF THIS SOFTWARE, EVEN IF ADVISED OF THE POSSIBILITY OF SUCH DAMAGE.
*******************************************************************************/

/*! @file
    @ingroup LTC6811-1
*/

/*
NOTES
 Setup:
   Set the terminal baud rate to 115200 and select the newline terminator.
   Ensure all jumpers on the demo board are installed in their default positions from the factory.
   Refer to Demo Manual DC2259.

USER INPUT DATA FORMAT:
 decimal : 1024
 hex     : 0x400
 octal   : 02000  (leading 0)
 binary  : B10000000000
 float   : 1024.0
 */

#include <Arduino.h>
#include <stdint.h>
#include "Linduino.h"
#include "LT_SPI.h"
//#include "LT_I2C.h"           // Hardware I2C driver
//#include "QuikEval_EEPROM.h"
#include "UserInterface.h"   // serial interface routines to communicate with the user
#include "LTC681x.h"
#include "LTC6811.h"
#include <SPI.h>

#define ENABLED 1
#define DISABLED 0

#define DATALOG_ENABLED 1
#define DATALOG_DISABLED 0

void print_menu();
void print_cells(uint8_t datalog_en);
void print_aux(uint8_t datalog_en);
void print_stat();
void print_open();
void print_config();
void print_rxconfig();
void print_comm();
void print_rxcomm();
void print_pwmconfig();
void print_rxpwmconfig();
void print_sctrl();
void print_rxsctrl(); 
void print_statsoc();
// void print_aux1();
void print_aux1(uint8_t datalog_en);
void check_error(int error);
void print_pec();
void serial_print_hex(uint8_t data);
char get_char();
void run_command(uint32_t cmd);
void measurement_loop(uint8_t datalog_en);

/**********************************************************
  Setup Variables
  The following variables can be modified to
  configure the software.
***********************************************************/
const uint8_t TOTAL_IC = 1;//!< Number of ICs in the daisy chain

//ADC Command Configurations. See LTC681x.h for options.
const uint8_t ADC_OPT = ADC_OPT_DISABLED; //!< ADC Mode option bit
const uint8_t ADC_CONVERSION_MODE = MD_7KHZ_3KHZ; //!< ADC Mode
const uint8_t ADC_DCP = DCP_ENABLED; //!< Discharge Permitted 
const uint8_t CELL_CH_TO_CONVERT = CELL_CH_ALL; //!< Channel Selection for ADC conversion
const uint8_t AUX_CH_TO_CONVERT = AUX_CH_ALL; //!< Channel Selection for ADC conversion
const uint8_t STAT_CH_TO_CONVERT = STAT_CH_ALL; //!< Channel Selection for ADC conversion
const uint8_t NO_OF_REG = REG_ALL; //!< Register Selection
const uint16_t MEASUREMENT_LOOP_TIME = 500; //!< Loop Time in milliseconds(ms)

//Under Voltage and Over Voltage Thresholds
const uint16_t OV_THRESHOLD = 41000; //!< Over voltage threshold ADC Code. LSB = 0.0001 ---(4.1V)
const uint16_t UV_THRESHOLD = 30000; //!< Under voltage threshold ADC Code. LSB = 0.0001 ---(3V)

//Loop Measurement Setup. These Variables are ENABLED or DISABLED. Remember ALL CAPS
const uint8_t WRITE_CONFIG = ENABLED; //!< Loop Measurement Setup
const uint8_t READ_CONFIG = ENABLED; //!< Loop Measurement Setup
const uint8_t MEASURE_CELL = ENABLED; //!< Loop Measurement Setup
const uint8_t MEASURE_AUX = ENABLED; //!< Loop Measurement Setup
const uint8_t MEASURE_STAT = ENABLED; //!< Loop Measurement Setup
const uint8_t PRINT_PEC = ENABLED; //!< Loop Measurement Setup
/************************************
  END SETUP
*************************************/

/******************************************************
 Global Battery Variables received from 681x commands.
 These variables store the results from the LTC6811
 register reads and the array lengths must be based
 on the number of ICs on the stack
 ******************************************************/
cell_asic bms_ic[TOTAL_IC]; //!< Global Battery Variable

/*********************************************************
 Set the configuration bits. 
 Refer to the Configuration Register Group from data sheet. 
**********************************************************/
bool REFON = true; //!< Reference Powered Up Bit
bool ADCOPT = false; //!< ADC Mode option bit
bool gpioBits_a[5] = {false,false,false,false,false}; //!< GPIO Pin Control // Gpio 1,2,3,4,5
uint16_t UV=UV_THRESHOLD; //!< Under-voltage Comparison Voltage
uint16_t OV=OV_THRESHOLD; //!< Over-voltage Comparison Voltage
bool dccBits_a[12] = {false,false,false,false,false,false,false,false,false,false,false,false}; //!< Discharge cell switch //Dcc 1,2,3,4,5,6,7,8,9,10,11,12
bool dctoBits[4] = {true, false, true, false}; //!< Discharge time value // Dcto 0,1,2,3 // Programed for 4 min 
/*Ensure that Dcto bits are set according to the required discharge time. Refer to the data sheet */

#include "pin_abstraction.h"
DigitalOut temp_sensor_ss(PA0);
DigitalOut active_balance_upper_ss(PB0);
DigitalOut active_balance_lower_ss(PB4);
DigitalOut led0(PC13);

/*!**********************************************************************
 \brief  Initializes hardware and variables
 @return void
 ***********************************************************************/
void setup()
{
  temp_sensor_ss = 0;
  active_balance_upper_ss = 0;
  active_balance_lower_ss = 0;
  led0 = 0;
  delay(1000);
  led0 = 1;

  Serial.begin(9600);
  // quikeval_SPI_connect();
  
  spi_enable(SPI_CLOCK_DIV128); // This will set the Linduino to have a 1MHz Clock
  LTC6811_init_cfg(TOTAL_IC, bms_ic);
  for (uint8_t current_ic = 0; current_ic<TOTAL_IC;current_ic++) 
  {
    LTC6811_set_cfgr(current_ic,bms_ic,REFON,ADCOPT,gpioBits_a,dccBits_a, dctoBits, UV, OV);
  }
  LTC6811_reset_crc_count(TOTAL_IC,bms_ic);
  LTC6811_init_reg_limits(TOTAL_IC,bms_ic);
  print_menu();
}

/*!*********************************************************************
 \brief Main loop
 @return void
***********************************************************************/
void loop()
{
  if (Serial.available())           // Check for user input
  {
    uint32_t user_command;
    user_command = read_int();      // Read the user command
    if(user_command=='m')
    { 
      print_menu();
    }
    else
    { 
      Serial.println(user_command);
      run_command(user_command); 
    }   
  }
}


/*!*****************************************
 \brief Executes the user command
 @return void
*******************************************/
void run_command(uint32_t cmd)
{
  const uint8_t STREG=0;
  int8_t error = 0;
  uint32_t conv_time = 0;
  uint32_t user_command;
  int8_t readIC=0;
  char input = 0;
  
  switch (cmd)
  {
    case 1: // Write and Read Configuration Register
      wakeup_sleep(TOTAL_IC);
      LTC6811_wrcfg(TOTAL_IC,bms_ic);
      print_config();
      wakeup_idle(TOTAL_IC);
      error = LTC6811_rdcfg(TOTAL_IC,bms_ic);
      check_error(error);
      print_rxconfig();
      break;

    case 2: // Read Configuration Register
      wakeup_sleep(TOTAL_IC);
      error = LTC6811_rdcfg(TOTAL_IC,bms_ic);
      check_error(error);
      print_rxconfig();
      break;

    case 3: // Start Cell ADC Measurement
      wakeup_sleep(TOTAL_IC);
      LTC6811_adcv(ADC_CONVERSION_MODE,ADC_DCP,CELL_CH_TO_CONVERT);
      conv_time = LTC6811_pollAdc();
      Serial.print(F("Cell conversion completed in:"));
      Serial.print(((float)conv_time/1000), 1);
      Serial.println(F("ms"));
      Serial.println();
      break;

    case 4: // Read Cell Voltage Registers
      wakeup_sleep(TOTAL_IC);
      error = LTC6811_rdcv(NO_OF_REG, TOTAL_IC,bms_ic); // Set to read back all cell voltage registers
      check_error(error);
      print_cells(DATALOG_DISABLED);
      break;

    case 5: // Start GPIO ADC Measurement
      wakeup_sleep(TOTAL_IC);
      LTC6811_adax(ADC_CONVERSION_MODE, AUX_CH_TO_CONVERT);
      conv_time = LTC6811_pollAdc();
      Serial.print(F("Aux conversion completed in: "));
      Serial.print(((float)conv_time/1000), 1);
      Serial.println(F(" ms"));    
      Serial.println(); 
      break;

    case 6: // Read AUX Voltage Registers
      wakeup_sleep(TOTAL_IC);
      error = LTC6811_rdaux(NO_OF_REG,TOTAL_IC,bms_ic); // Set to read back all aux registers
      check_error(error);
      print_aux(DATALOG_DISABLED);
      break;

    case 7: // Start Status ADC Measurement
      wakeup_sleep(TOTAL_IC);
      LTC6811_adstat(ADC_CONVERSION_MODE, STAT_CH_TO_CONVERT);
      conv_time=LTC6811_pollAdc();
      Serial.print(F("Stat conversion completed in "));
      Serial.print(((float)conv_time/1000), 1);
      Serial.println(F(" ms"));
      Serial.println();
      break;

    case 8: // Read Status registers
      wakeup_sleep(TOTAL_IC);
      error = LTC6811_rdstat(NO_OF_REG,TOTAL_IC,bms_ic); // Set to read back all aux registers
      check_error(error);
      print_stat();
      break;

    case 9:// Start Combined Cell Voltage and GPIO1, GPIO2 Conversion and Poll Status
      wakeup_sleep(TOTAL_IC);
      LTC6811_adcvax(ADC_CONVERSION_MODE,ADC_DCP);
      conv_time = LTC6811_pollAdc();
      Serial.println(F("Start Combined Cell Voltage and GPIO1, GPIO2 conversion completed"));
      Serial.print(F("conversion completed in:"));
      Serial.print(((float)conv_time/1000), 1);
      Serial.println(F("ms"));
      Serial.println();
      wakeup_idle(TOTAL_IC);
      error =LTC6811_rdcv(NO_OF_REG, TOTAL_IC,bms_ic); // Set to read back all cell voltage registers
      check_error(error);
      print_cells(DATALOG_DISABLED);     
      wakeup_idle(TOTAL_IC);
      error = LTC6811_rdaux(NO_OF_REG,TOTAL_IC,bms_ic); // Set to read back all aux registers
      check_error(error);
      print_aux1(DATALOG_DISABLED);
      Serial.println();
      break;
      
    case 10: //Start Combined Cell Voltage and Sum of cells
      wakeup_sleep(TOTAL_IC);
      LTC6811_adcvsc(ADC_CONVERSION_MODE,ADC_DCP);
      conv_time = LTC6811_pollAdc();
      Serial.print(F("Combined Cell Voltage conversion completed in:"));
      Serial.print(((float)conv_time/1000), 1);
      Serial.println(F("ms"));
      Serial.println();
      wakeup_idle(TOTAL_IC);
      error = LTC6811_rdcv(NO_OF_REG, TOTAL_IC,bms_ic); // Set to read back all cell voltage registers
      check_error(error);
      print_cells(DATALOG_DISABLED);
      wakeup_idle(TOTAL_IC);
      error = LTC6811_rdstat(NO_OF_REG,TOTAL_IC,bms_ic); // Set to read back all stat registers
      check_error(error);
      print_statsoc();
      Serial.println();
      break;
      
    case 11: // Loop Measurements without data-log output
      Serial.println(F("transmit 'm' to quit"));
      wakeup_sleep(TOTAL_IC);
      LTC6811_wrcfg(TOTAL_IC,bms_ic);
      while (input != 'm')
      {
        if (Serial.available() > 0)
        {
          input = read_char();
        }

        measurement_loop(DATALOG_DISABLED);

        delay(MEASUREMENT_LOOP_TIME);
      }
      print_menu();
      break;

    case 12: //Data-log print option Loop Measurements
      Serial.println(F("transmit 'm' to quit"));
      wakeup_sleep(TOTAL_IC);
      LTC6811_wrcfg(TOTAL_IC,bms_ic);
      while (input != 'm')
      {
        if (Serial.available() > 0)
        {
          input = read_char();
        }

        measurement_loop(DATALOG_ENABLED);

        delay(MEASUREMENT_LOOP_TIME);
      }
      print_menu();
      break;

    case 13: // Run the Mux Decoder Self Test
      wakeup_sleep(TOTAL_IC);
      LTC6811_diagn();
      conv_time = LTC6811_pollAdc();
      Serial.print(F("DIAGN  conversion completed in: "));
      Serial.print(((float)conv_time/1000), 1);
      Serial.println(F(" ms"));    
      Serial.println(); 
      error = LTC6811_rdstat(NO_OF_REG,TOTAL_IC,bms_ic); // Set to read back all aux registers
      check_error(error);
      for (int ic = 0; ic<TOTAL_IC; ic++)
        { error = 0;
          Serial.print(" IC ");
          Serial.println(ic+1,DEC);
          if (bms_ic[ic].stat.mux_fail[0] != 0) error++;
        
          if (error==0) Serial.println(F("Mux Test: PASS "));
          else Serial.println(F("Mux Test: FAIL "));
        }
      Serial.println("");  
      break;

    case 14:  // Run the ADC/Memory Self Test
      wakeup_sleep(TOTAL_IC);
      error = LTC6811_run_cell_adc_st(CELL,TOTAL_IC,bms_ic, ADC_CONVERSION_MODE, ADCOPT);
      Serial.print(error, DEC);
      Serial.println(F(" : errors detected in Digital Filter and CELL Memory \n"));

      wakeup_sleep(TOTAL_IC);
      error = LTC6811_run_cell_adc_st(AUX,TOTAL_IC, bms_ic, ADC_CONVERSION_MODE, ADCOPT);
      Serial.print(error, DEC);
      Serial.println(F(" : errors detected in Digital Filter and AUX Memory \n"));

      wakeup_sleep(TOTAL_IC);
      error = LTC6811_run_cell_adc_st(STAT,TOTAL_IC, bms_ic, ADC_CONVERSION_MODE, ADCOPT);
      Serial.print(error, DEC);
      Serial.println(F(" : errors detected in Digital Filter and STAT Memory \n"));
      print_menu();
      break;
      
    case 15: // Run ADC Overlap self test
      wakeup_sleep(TOTAL_IC);
      error = (int8_t)LTC6811_run_adc_overlap(TOTAL_IC,bms_ic);
      if (error==0) Serial.println(F("Overlap Test: PASS "));
      else Serial.println(F("Overlap Test: FAIL"));
      Serial.println(); 
      break;

    case 16: // Run ADC Redundancy self test
      wakeup_sleep(TOTAL_IC);
      error = LTC6811_run_adc_redundancy_st(ADC_CONVERSION_MODE,AUX,TOTAL_IC, bms_ic);
      Serial.print(error, DEC);
      Serial.println(F(" : errors detected in AUX Measurement \n"));

      wakeup_sleep(TOTAL_IC);
      error = LTC6811_run_adc_redundancy_st(ADC_CONVERSION_MODE,STAT,TOTAL_IC, bms_ic);
      Serial.print(error, DEC);
      Serial.println(F(" : errors detected in STAT Measurement \n"));
      break;

    case 17: // Open Wire test for single cell detection
      wakeup_sleep(TOTAL_IC);         
      LTC6811_run_openwire_single(TOTAL_IC, bms_ic);
      print_open();
      Serial.println();    
      break;

    case 18: // Open Wire test for multiple cell and two consecutive cells detection
      wakeup_sleep(TOTAL_IC);         
      LTC6811_run_openwire_multi(TOTAL_IC, bms_ic);
      Serial.println();    
      break;

    case 19:// PEC Errors Detected
      print_pec(); 
      Serial.println();     
      break;

    case 20: //Reset PEC Counter
      LTC6811_reset_crc_count(TOTAL_IC,bms_ic);
      Serial.println(F("PEC counter reset"));
      Serial.println();
      break;
      
    case 21: // Enable a discharge transistor
      Serial.println(F("Please enter the Spin number:"));
      readIC = (int8_t)read_int();
      Serial.println(readIC);
      wakeup_sleep(TOTAL_IC);
      LTC6811_set_discharge(readIC,TOTAL_IC,bms_ic);
      LTC6811_wrcfg(TOTAL_IC,bms_ic);   
      print_config();
      wakeup_idle(TOTAL_IC);
      error = LTC6811_rdcfg(TOTAL_IC,bms_ic);
      check_error(error);
      print_rxconfig();
      break;
      
    case 22: // Clear all discharge transistors
      wakeup_sleep(TOTAL_IC);
      LTC6811_clear_discharge(TOTAL_IC,bms_ic);
      LTC6811_wrcfg(TOTAL_IC,bms_ic);    
      print_config();
      wakeup_idle(TOTAL_IC);
      error = LTC6811_rdcfg(TOTAL_IC,bms_ic);
      check_error(error);
      print_rxconfig();
      break;

    case 23://Write read pwm configuration     
      /*****************************************************
         PWM configuration data.
         1)Set the corresponding DCC bit to one for pwm operation. 
         2)Set the DCTO bits to the required discharge time.
         3)Choose the value to be configured depending on the
          required duty cycle. 
         Refer to the data sheet. 
      *******************************************************/ 
      wakeup_sleep(TOTAL_IC);
      for (uint8_t current_ic = 0; current_ic<TOTAL_IC;current_ic++) 
      {
        bms_ic[current_ic].pwm.tx_data[0]= 0x88; // Duty cycle for S pin 2 and 1
        bms_ic[current_ic].pwm.tx_data[1]= 0x88; // Duty cycle for S pin 4 and 3
        bms_ic[current_ic].pwm.tx_data[2]= 0x88; // Duty cycle for S pin 6 and 5
        bms_ic[current_ic].pwm.tx_data[3]= 0x88; // Duty cycle for S pin 8 and 7
        bms_ic[current_ic].pwm.tx_data[4]= 0x88; // Duty cycle for S pin 10 and 9
        bms_ic[current_ic].pwm.tx_data[5]= 0x88; // Duty cycle for S pin 12 and 11
      }          
      LTC6811_wrpwm(TOTAL_IC,0,bms_ic);
      print_pwmconfig(); 

      wakeup_idle(TOTAL_IC);
      LTC6811_rdpwm(TOTAL_IC,0,bms_ic);       
      print_rxpwmconfig();                              
      break;

    case 24: // Write and read S Control Register Group
      wakeup_sleep(TOTAL_IC);
      /**************************************************************************************
         S pin control. 
         1)Ensure that the pwm is set according to the requirement using the previous case.
         2)Choose the value depending on the required number of pulses on S pin. 
         Refer to the data sheet. 
      ***************************************************************************************/
      for (uint8_t current_ic = 0; current_ic<TOTAL_IC;current_ic++) 
      {
        bms_ic[current_ic].sctrl.tx_data[0]=0xFF; // No. of high pulses on S pin 2 and 1
        bms_ic[current_ic].sctrl.tx_data[1]=0xFF; // No. of high pulses on S pin 4 and 3
        bms_ic[current_ic].sctrl.tx_data[2]=0xFF; // No. of high pulses on S pin 6 and 5
        bms_ic[current_ic].sctrl.tx_data[3]=0xFF; // No. of high pulses on S pin 8 and 7
        bms_ic[current_ic].sctrl.tx_data[4]=0xFF; // No. of high pulses on S pin 10 and 9
        bms_ic[current_ic].sctrl.tx_data[5]=0xFF; // No. of high pulses on S pin 12 and 11
      }
      LTC6811_wrsctrl(TOTAL_IC,STREG,bms_ic);
      print_sctrl();

      // Start S Control pulsing
      wakeup_idle(TOTAL_IC);
      LTC6811_stsctrl();
      LTC6811_pollAdc();
      Serial.println(F("Start S Control Pulsing"));
      Serial.println();

      // Read S Control Register Group 
      wakeup_idle(TOTAL_IC);
      error=LTC6811_rdsctrl(TOTAL_IC,STREG,bms_ic);
      check_error(error);
      print_rxsctrl();
      break;

    case 25: // Clear S Control Register Group
      wakeup_sleep(TOTAL_IC);
      LTC6811_clrsctrl();
      Serial.println(F("S Control Register Cleared"));
      Serial.println(); 
      
      // Read S Control Register Group
      wakeup_idle(TOTAL_IC);
      error=LTC6811_rdsctrl(TOTAL_IC,STREG,bms_ic);
      check_error(error);
      print_rxsctrl();
      break;

    // case 26://Start SPI Communication on the GPIO Ports
    //   wakeup_sleep(TOTAL_IC);
    //   /************************************************************
    //      Communication control bits and communication data bytes. 
    //      Refer to the data sheet. 
    //   *************************************************************/  
    //    for (uint8_t current_ic = 0; current_ic<TOTAL_IC;current_ic++) 
    //   {                        
    //     bms_ic[current_ic].com.tx_data[0]= 0x80;
    //     bms_ic[current_ic].com.tx_data[1]= 0x00;
    //     bms_ic[current_ic].com.tx_data[2]= 0xA2;
    //     bms_ic[current_ic].com.tx_data[3]= 0x20;
    //     bms_ic[current_ic].com.tx_data[4]= 0xA3;
    //     bms_ic[current_ic].com.tx_data[5]= 0x39;
    //   }    
    //   LTC6811_wrcomm(TOTAL_IC,bms_ic);               
    //   print_comm();   

    //   wakeup_idle(TOTAL_IC);
    //   LTC6811_stcomm(); 
    //   LTC6811_pollAdc();           
    //   Serial.println(F("Stcomm SPI Communication completed"));
    //   Serial.println();  

    //   wakeup_idle(TOTAL_IC);
    //   error = LTC6811_rdcomm(TOTAL_IC,bms_ic);                       
    //   check_error(error);
    //   print_rxcomm();        
    //   break;

    // case 27: // write byte I2C Communication on the GPIO Ports(using eeprom 24AA01)
    //   wakeup_sleep(TOTAL_IC);
    //   /************************************************************
    //      Communication control bits and communication data bytes. 
    //      Refer to the data sheet. 
    //   *************************************************************/ 
    //   for (uint8_t current_ic = 0; current_ic<TOTAL_IC;current_ic++) 
    //   {
    //     bms_ic[current_ic].com.tx_data[0]= 0x6A; // Icom(6)Start + I2C_address D0 (1010 0000)
    //     bms_ic[current_ic].com.tx_data[1]= 0x00; // Fcom master ack  
    //     bms_ic[current_ic].com.tx_data[2]= 0x00; // eeprom address D1 (0000 0000)
    //     bms_ic[current_ic].com.tx_data[3]= 0x00; // Fcom master ack 
    //     bms_ic[current_ic].com.tx_data[4]= 0x01; // Icom BLANCK D2 (0Xxx)
    //     bms_ic[current_ic].com.tx_data[5]= 0x29; // Fcom master nack+stop 
    //   }             
             
    //   LTC6811_wrcomm(TOTAL_IC,bms_ic);// write comm register    
    //   print_comm();
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

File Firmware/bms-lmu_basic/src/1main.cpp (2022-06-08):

// #include <Arduino.h>
// #include "bms_lmu.h"
// #include "SPI.h"
// #include <eXoCAN.h>
// #include "TickerInterrupt.h"
// #include "PBalancer.h"

// /******************************************************************************
//  * BMS_LMU - HARDWARE REVISION 0
//  * Patrick Curtain & Ethan Suter
//  * 
//  * Battery Management System - Local Measurement Unit
//  * 
//  * An active balancer created for FYRP by Patrick Curtain and Ethan Suter, 
//  * Semester 2 2021 and Semester 1 2022, at Swinburne University of Technology.
//  * 
//  * Code base derived from Team Swinburne FSAE
//  * Available: https://github.com/Team-Swinburne/ts_20-code-development
//  * 
//  * Revision     Date      Comments
//  * --------   --------    --------
//  * 0.0        28/5/2022   Initial Code Base
//  * 
//  * 
// ******************************************************************************/

// #define HW_REV "0"
// #define SW_REV "0.0"

// // PINOUT
// #define LED0 PC13
// #define CAN_TX_LED PB5
// #define CAN_RX_LED PB6
// #define SPI_TX_LED PB7
// #define SPI_RX_LED PB8
// #define FAULT_RELAY PA9
// #define FAULT_RELAY_FEEDBACK PA10

// // NOT SAFETY PARAMETERS
// #define DISCHARGE_TIMER_LIMIT 1000
// #define HEART_RATE 1000
// #define CAN_INTERVAL 800
// #define CANBUS_FREQUENCY 250000

// #define TX_ADDRESS 0x481

// // led pins
// DigitalOut can_tx_led(CAN_TX_LED);
// DigitalOut can_rx_led(CAN_TX_LED);
// DigitalOut spi_tx_led(CAN_TX_LED);
// DigitalOut spi_rx_led(CAN_TX_LED);

// // Globals
// Heartbeat heartbeat(FAULT_RELAY, FAULT_RELAY_FEEDBACK, LED0);
// Stack stack;
// PBalancer passive_balancer(stack, DISCHARGE_TIMER_LIMIT);

// // Interfaces
// eXoCAN can;

// // Timers
// TickerInterrupt ticker(TIM2, 1);

// struct msg_frame
// {
//   uint8_t len = 8;
//   uint8_t bytes[8] = {0};
// };

// static msg_frame	heart_frame {.len = 3},
//                	bms_lower_bank {.len = 6}, 
// 				        bms_upper_bank {.len = 6},
//                	temperature {.len = 8};

// uint8_t rxData[8];

// void can_tx(){
//   can.transmit(TX_ADDRESS, heart_frame.bytes, heart_frame.len);
//   can.transmit(TX_ADDRESS + 1, bms_lower_bank.bytes, bms_lower_bank.len);
//   can.transmit(TX_ADDRESS + 2, bms_upper_bank.bytes, bms_upper_bank.len);
//   can.transmit(TX_ADDRESS + 3, temperature.bytes, temperature.len);

//   can_tx_led = !can_tx_led;
// }

// // Can receive interupt service routine
// void canISR() {
// 	can.rxMsgLen = can.receive(can.id, can.fltIdx, can.rxData.bytes);
// }


// void can_rx() {
// 	if (can.rxMsgLen > -1) {
//     can_rx_led = !can_rx_led;
// 	}
// }

// uint8_t array_to_uint8(bool arr[], int count){
//     int ret = 0;
//     int tmp;
//     for (int i = 0; i < count; i++) {
//         tmp = arr[i];
//         ret |= tmp << (count - i - 1);
//     }
//     return ret;
// }

// uint16_t check_errors(){
//   bool error_code[8];

// 	error_code[ERROR_OV_FAULT] = stack.ov_fault();
// 	error_code[ERROR_UV_FAULT] = stack.uv_fault();
// 	// error_code[ERROR_OT_FAULT] = !imd.get_IMD_ok();
// 	error_code[ERROR_RELAY_FAULT] = heartbeat.relay_fault();
	
// 	// error_code[ERROR_ORION_LOW_VOTLAGE] 	= orion.check_low_voltage();
// 	// error_code[ERROR_ORION_HIGH_VOLTAGE] 	= orion.check_high_voltage();
// 	// error_code[ERROR_ORION_OVERTEMPERATURE] = orion.check_overtemperature();
// 	// error_code[ERROR_PERIPHERALS] = 0;

// 	return array_to_uint8(error_code, 8);
// }

// void update_can_frames(){
//   heart_frame.bytes[0] = heartbeat.state();
//   heart_frame.bytes[0] = heartbeat.counter();
//   heart_frame.bytes[1] = heartbeat.fault_code();

//   for (int i = 0; i < 6; i++){
//     bms_lower_bank.bytes[i] = stack.cell_voltage(i);
//   }

//   for (int i = 6; i < 12; i++){
//     bms_upper_bank.bytes[i] = stack.cell_voltage(i);
//   }

//   // add in the temp measurement thing.
// }

// void state_d(){

//   update_can_frames();
//   heartbeat.fault_code(check_error());

//   switch(heartbeat.state()) {
    
//     case (FAULT):
//       // do nothing, clear the error as quickly
//       // as possible.
//       if (check_errors() == 0){
//         heartbeat.state(IDLE);
//       }
//       break;
    
//     case (IDLE):
//       // literally do nothing!
//       break;
    
//     case (ACTIVE_BALANCING):
//       // not sure yet!
//       // push into passive state once done
//       break;
    
//     case (PASSIVE_BALANCING):
//       passive_balancer.start_balance();
//       break;
    
//   }
// }

// void start_up_lights(){
//   pinMode(PB5, OUTPUT);
//   pinMode(PB6, OUTPUT);
//   pinMode(PB7, OUTPUT);
//   pinMode(PB8, OUTPUT);

//   int scroller_time = 100;
//   digitalWrite(PB5, HIGH);
//   delay(scroller_time);
//   digitalWrite(PB6, HIGH);
//   delay(scroller_time);
//   digitalWrite(PB7, HIGH);
//   delay(scroller_time);
//   digitalWrite(PB8, HIGH);
//   delay(scroller_time);

//   digitalWrite(PB5, LOW);
//   delay(scroller_time);
//   digitalWrite(PB6, LOW);
//   delay(scroller_time);
//   digitalWrite(PB7, LOW);
//   delay(scroller_time);
//   digitalWrite(PB8, LOW);
//   delay(scroller_time);
// }


// // timer functions
// void heartbeat_cb(){
//   heartbeat.tick(check_errors());
// }

// void setup() {

//   // setup the serial.
//   Serial.begin(9600);
//   Serial.print("Starting BMS-LMU \n");
//   Serial.print("  HARDWARE REVISION - 0\n");
//   Serial.print("  SOFTWARE REVISION - 0.0\n\n");
//   Serial.print("Swinburne University of Technology - FYRP40002\n  Patrick Curtain \& Ethan Suter\n");

//   // setup the can
//   can.begin(STD_ID_LEN, CANBUS_FREQUENCY, PORTA_11_12_WIRE_PULLUP);   //11 Bit Id, 500Kbps
//   // can.filterMask16Init(0, 0x600, 0x7ff);
//   can.attachInterrupt(canISR);
  
//   // setup heartbeat tickers.
//   ticker.start();
//   ticker.attach(heartbeat_cb, HEART_RATE);

//   // start up the pbalancer
//   passive_balancer.setup();

//   ticker.attach(can_tx, CAN_INTERVAL);

//   // finished boot, flash the lights to confirm startup!
//   start_up_lights();
//   Serial.print("Finished boot! Starting\n");

//   Serial.begin(9600);
    
//     #define adSS PA0
//   pinMode(adSS, OUTPUT);
//   digitalWrite(adSS, HIGH);

//   SPI.begin();
// }

// DigitalOut temp_sensor_ss(PA0);
// DigitalOut active_balance_upper_ss(PB0);
// DigitalOut active_balance_lower_ss(PB4);
// DigitalOut passive_balance_ss(PA1);


// void loop() {

//     temp_sensor_ss = 0;
//     active_balance_upper_ss = 1;
//     active_balance_lower_ss = 1;
//     passive_balance_ss = 1;

// byte commandByte;
//   byte result[2];
  
//   for(byte x=0;x<8;x++) {
//     // set to adc# and bit3 HIGH
//     commandByte = x + 8;
//     // shift into position
//     commandByte = commandByte << 4;
//     // set low 4 bits HIGH
//     commandByte = commandByte | 0x0f;   

//     // enable ADC SPI slave select
//     digitalWrite(adSS, LOW);
//     delayMicroseconds(1);
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
